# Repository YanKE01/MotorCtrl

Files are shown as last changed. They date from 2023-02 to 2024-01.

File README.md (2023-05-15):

# 光伏水泵评估套件

  

## 开发环境

HardWare：STMicroelectronics Series MCU

SoftWare：KEIL V5/4, CUBEMX , VsCode

## 支持电机

- [x] BLDC+HALL Sensor. Ref: MotorCtrl\SoftWare\BLDC\F407IGT6_HALL
- [x] BLDC SensorLess. Ref: MotorCtrl\SoftWare\BLDC\F407IGT6_NOHALL
- [x] 48V PMSM. Ref: MotorCtrl\SoftWare\PMSM\MCSDK\F401RET6_Pump

## 目录说明

Doc：存放文档

HardWare：存放硬件图纸

Record：存放项目记录

SoftWare：存放软件控制方案

## 开源项目支持

SimpleFoc: [SimpleFoc官网](https://simplefoc.com/)

Ctrl-Foc-Lite: [Ctrl-Foc-Lite项目](https://github.com/peng-zhihui/Ctrl-FOC-Lite)

STM32 MCSDK: [STM32电机库官网](https://www.st.com/content/st_com/en/products/embedded-software/mcu-mpu-embedded-software/stm32-embedded-software/stm32cube-expansion-packages/x-cube-mcsdk.html)

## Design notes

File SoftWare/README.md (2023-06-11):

# SoftWare文件夹说明

* BLDC：存放BLDC电机Hall, SensorLess相关代码
* PMSM：存放PMSM电机无感控制相关代码
* Matlab：存放Matlab仿真实验代码
* Fortior: 存放基于FU6861Q的无感FOC相关代码
* LCM_FOC:存放领芯控制方案
* test:临时测试代码，误动

## Record

母线电压在52V左右时，电机带负载转数拉到3700RPM，电流16A左右，难道电机已经跑到了800W????

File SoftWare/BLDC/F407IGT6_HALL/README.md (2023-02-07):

# 基于正点原子开发版的HALL BLDC驱动

## 开发环境

* CUBEMX: 6.7.0
* KEIL: 5.28.0

## 测试硬件



## 实验效果

* 按下KEY0实现增速
* 按下KEY1实现减速
* 按下KEY2停止电机

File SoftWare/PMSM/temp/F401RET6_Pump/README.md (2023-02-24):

# MCSDK

### 功能指标



### 电机参数修改

* 电机参数：Inc\pmsm_motor_parameters.h
* 电源参数：Inc\power_stage_parameters.h

### 工程问题记录

* TM1650上电不显示：TM1650芯片内部初始化并未完成，所以Delay一段时间，等TM1650内部启动完成。

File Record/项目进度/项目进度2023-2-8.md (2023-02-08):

# BLDC/PMSM开发事项确认

### 人员

人员安排？

### PMSM

* 光伏水泵是否合板？
* 是否按原定的数码管+按键组合?
* 项目时间点确认？
* 优先基于24VPMSM电机进行原理性测试？

### BLDC

以基于正点PCB确认可行性。

* 后续原理图与PCB安排？

### 材料

* 线电感：数字电桥测量，需要购买？

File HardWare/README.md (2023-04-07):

# 硬件问题汇总

- [ ] TM1650面板PCB，以飞线，未修复。
- [ ] 驱动板5V供电部分错误，以割线，未修复。
- [ ] 驱动板三相电流未开窗。
- [ ] 3倍耐压MOS未更换。

### 修改后及时同步仓库

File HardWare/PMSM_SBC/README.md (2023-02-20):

# PMSM_SBC

### 版本迭代

当前版本：PMSM_Driver_V0.16



### 绘制人员

* 设计：严柯
* 绘制：王建
* 审核：傅雷

### 日志

* LMV358以替换TP2412，原LMV358启动失败次数过多，引脚兼容，无需修改PCB

### 其他

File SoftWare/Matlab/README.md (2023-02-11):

# FOC MATLAB仿真

## 1.初期ANTI PARK仿真实验的相关设置

* 模拟电角度增加可以使用Repeating Sequence模块搭建



* 仿真时间与离散化设置







## 2.电流环





电流闭环系统如下：



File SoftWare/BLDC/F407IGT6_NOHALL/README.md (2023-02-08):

# 基于正点原子开发版的BLDC 无感驱动

## 开发环境

* CUBEMX: 6.7.0
* KEIL: 5.28.0

## 测试硬件

* 务必将驱动板板载跳线由HALL<->H&Z 切换至 ==H&Z <-> ZERO==

## 开发记录



顺时针：HallLess的状态为 5 4 6 2 3 1



逆时针：HallLess的状态为 5 1 3 2 6 4



## 实验效果

* 按下KEY0实现逆时针旋转
* 按下KEY1实现顺时针旋转
* 按下KEY2停止电机

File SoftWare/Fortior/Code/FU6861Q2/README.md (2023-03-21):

# Standard Software for Vacuum Cleaners

> 这是基于FU6861Q2的单电阻无感FOC标准吸尘器程序  
> 如有BUG或者优化建议，可提交到标准程序对应的议题

## 适用编译器

- [支持] KeilC51
- [不支持] FTCC

## 适用芯片
- FU6861Q2

## 发布记录

V1.0.0(2022-11-29)
- 初始版本
- 基于FU6861Q2的单电阻无感FOC标准吸尘器程序
---

## 版权说明
> 版权所有©峰岹科技（深圳）股份有限公司（以下简称：峰岹科技）。<br>

> 为改进设计和/或性能，峰岹科技保留对本文档所描述或包含的产品（包括电路、标准元件和/><br>或软件）进行更改的权利。本文档中包含的信息供峰岹科技的客户进行一般性使用。峰岹科技的客户应确保采取适当行动，以使其对峰岹科技产品的使用不侵犯任何专利。峰岹科技尊重第三方的有效专利权，不侵犯或协助他人侵犯该等权利。<br>
> 本文档版权归峰岹科技所有，未经峰岹科技明确书面许可，任何单位及个人不得以任何形式或方式（如电子、机械、磁性、光学、化学、手工操作或其他任何方式），对本文档任何内容进行复制、传播、抄录、存储于检索系统或翻译为任何语种，亦不得更改或删除> 本内容副本中的任何版权或其他声明信息。<br>

> 峰岹科技（深圳）股份有限公司<br>
> 深圳市南山区科技中二路深圳软件园二期11栋2楼203<br>
> 邮编：518057<br>
> 电话：0755-26867710<br>
> 传真：0755-26867715<br>
> 网址：[www.fortiortech.com](https://www.fortiortech.com)

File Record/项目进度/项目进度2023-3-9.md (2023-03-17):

* MOS选型：耐压选择超过三倍。参考样品的选择。

* 时间计划表。
* 散热问题。
* 外观：
  * 铝壳公模，可购买
  * 按照样品来
* 功能测试：按照实物来、实机测试。
* 转速问题：4200RPM为额定点。
* 处理：观测器调整。
  * 电流上去后，观测器没处理好。
  * 库方案没有处理。
* 电机制作粗糙，只能调试。

# 后期进度安排：

1. 外壳设计

2. 走线设计 有参考设计。参照设计

3. MOS管选型

4. 给出电机需要参数

5. 电机加负载 (放在水里) 

6. 电源：兆信。电源串

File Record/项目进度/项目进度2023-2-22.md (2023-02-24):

# 2023-2-22项目进度记录

### 现有问题：

* 转速无法上升到2300以上，疑似11V稳压输出不行。
* 显示面板需要上电复位后，才显示。(以修复PCB错误)

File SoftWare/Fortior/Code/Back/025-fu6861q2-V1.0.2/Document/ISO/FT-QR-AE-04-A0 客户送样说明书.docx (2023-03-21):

客户送样说明书

送样日期：2020年5月2日

1、 基本情况

供 应 方： | 峰岹科技（深圳）股份有限公司 | 工 程 师： | 汤工：13856094270
接 收 方： | 新科空调有限公司 | 工 程 师： | 刘工
项目名称： | 压缩机 | 产品型号： | FU6812L
配件清单： | FU6812L控制板（1pcs）、电机接头线(1条)

二、测试板基本功能描述

序号 | 项目 | 参数 | 序号 | 项目 | 参数
1 | 电机规格型号 | 极对数为3、电阻0.35欧姆，电感为0.00005H | 2 | 负载
3 | 工作电压（V） | 220V交流电 | 4 | 工作电流（A） | 最大10A
其他

三、连线说明

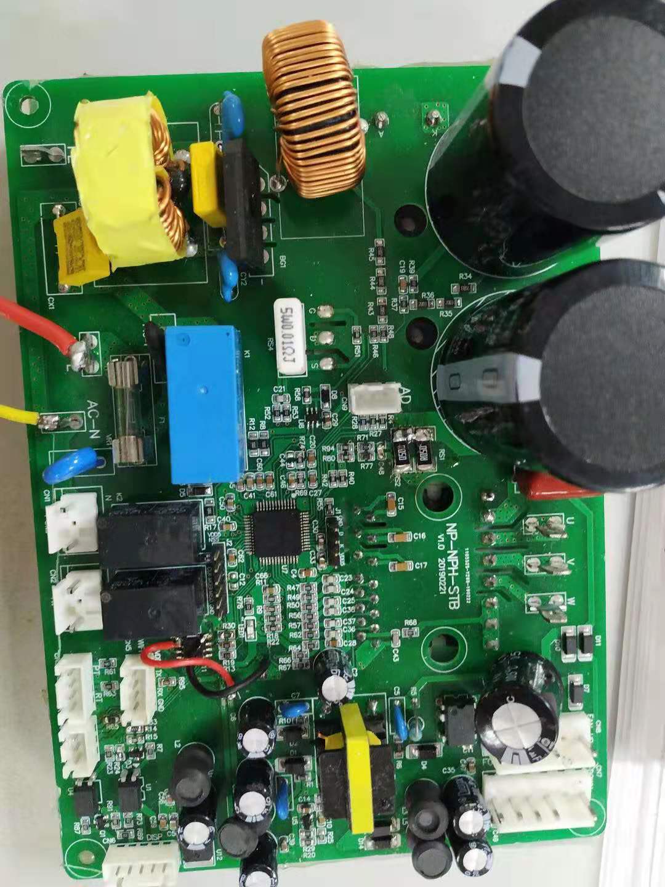
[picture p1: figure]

电机U,V,W相线

220VAC接线端

峰岹科技（深圳）股份有限公司

表单编号：FT-QR-AE-04-A0 流水号：

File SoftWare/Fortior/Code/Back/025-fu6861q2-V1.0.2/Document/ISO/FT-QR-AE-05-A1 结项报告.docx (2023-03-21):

# 项目结项报告

结项日期：2020年12月05日

一、项目结项信息

应用方案描述：新科空调 | 项目当前阶段: 结项
结项原因：客户持续2个月以上无反馈 | 申请人：汤伟
销售审核人： | 应用审核人：

备注：应用方案结项原因有以下几种情况：

（1）符合要求，已经量产；

（2）在方案设计及产品板内部测试阶段遇到无法解决的技术问题；

（3）在客户端测试验证阶段出现无法解决的异常情况；

（4）因性能、价格、交期达不到客户要求；

（5）客户持续2个月以上无反馈；

（6）客户已确认性能符合要求，但未有订单；

（7）其他__________________________。

二、结项清单

客户方案性能设计需求表 | √
应用方案计划表 | √
客户产品板测试报告 | √
客户送样说明书 | √
成功案例介绍PPT（必要时） | ×
烧录文件归档 | ×
原理图&PCB归档 | √

峰岹科技（深圳）股份有限公司

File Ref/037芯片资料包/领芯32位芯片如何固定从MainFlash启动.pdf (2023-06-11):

## 领芯 32 位芯片如何固定从 MainFlash 启动

## 1，确认芯片 BOOT 模式

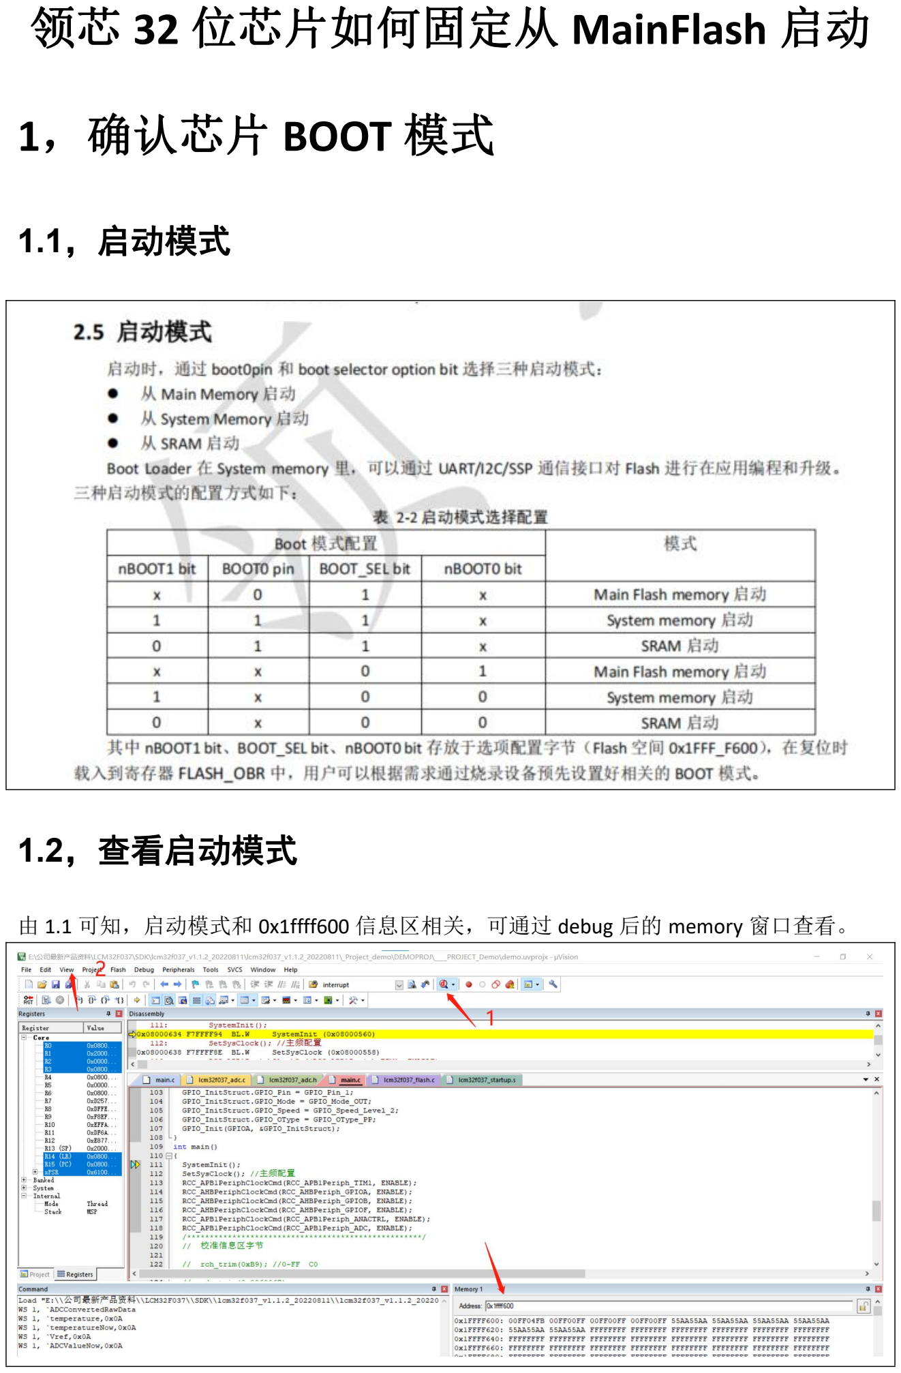
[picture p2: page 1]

1.1，启动模式

1.2，查看启动模式

由 1.1 可知，启动模式和 0x1ffff600 信息区相关，可通过 debug 后的 memory 窗口查看。

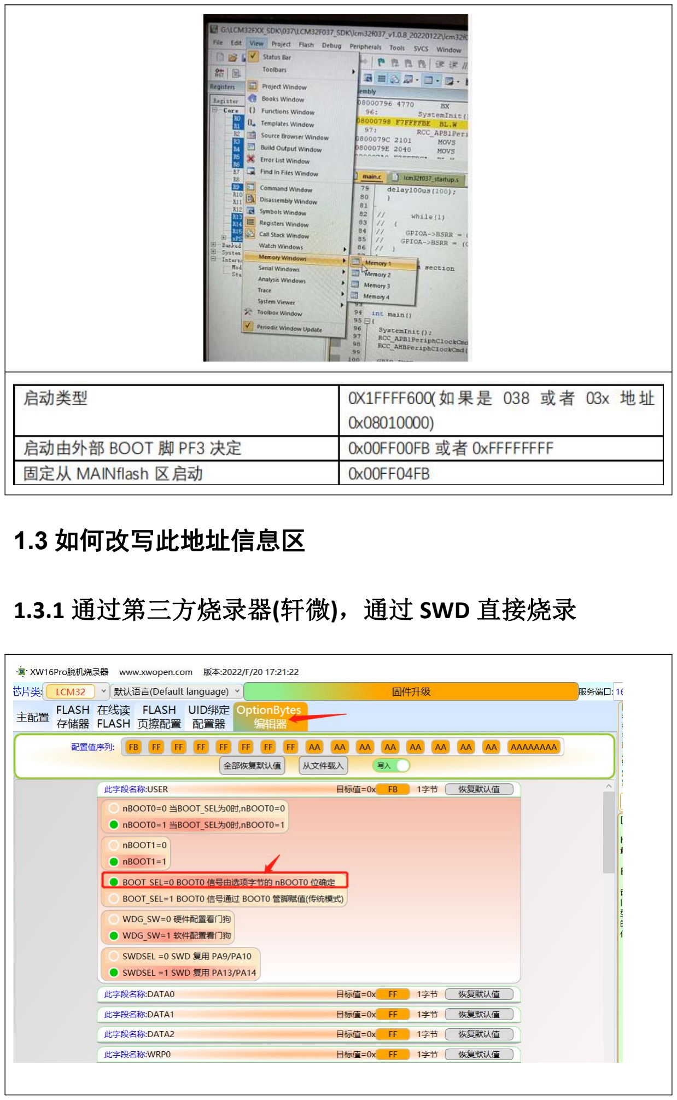
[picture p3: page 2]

### 1.3 如何改写此地址信息区

### 1.3.1 通过第三方烧录器(轩微)，通过 SWD 直接烧录

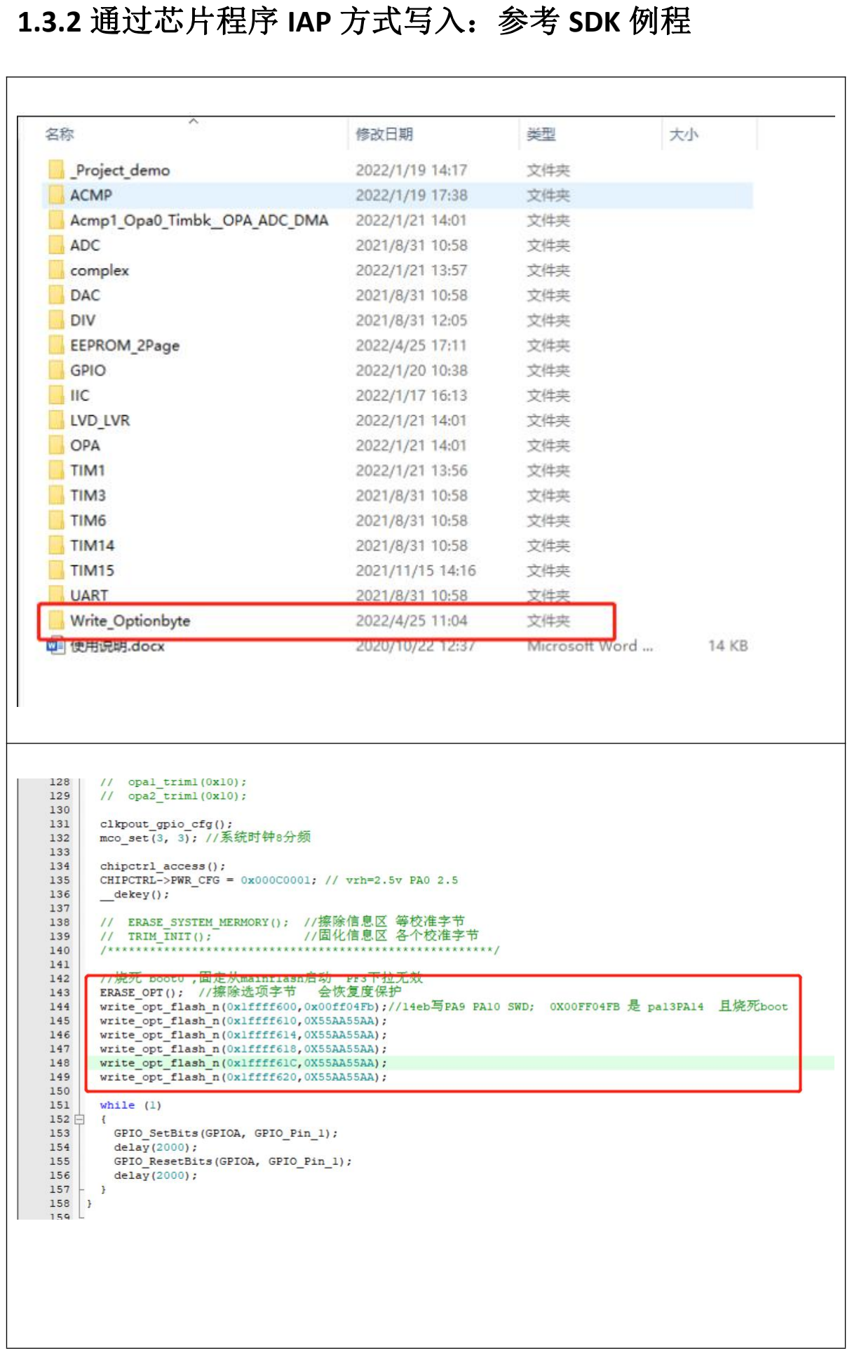
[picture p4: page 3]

### 1.3.2 通过芯片程序 IAP 方式写入：参考 SDK 例程

此方式是程序自写，下载此程序，PF3 拉低，确保此程序正

常运行。运行结束后使用 DEBUG 确认数据。

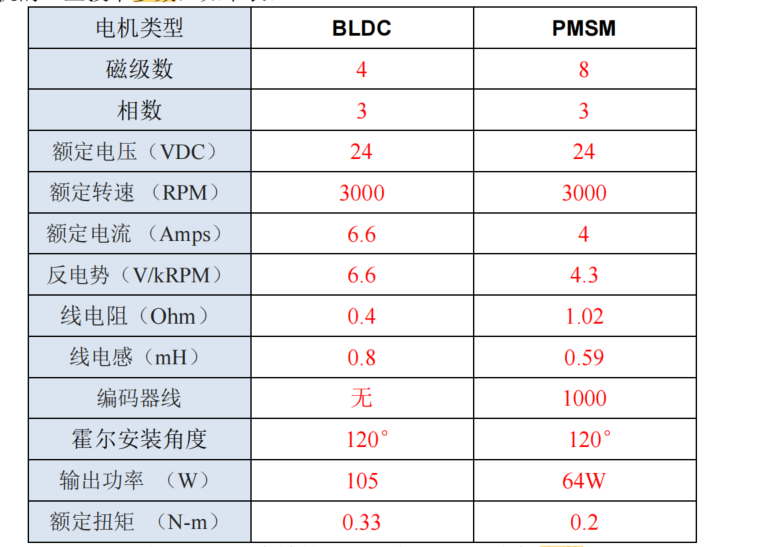
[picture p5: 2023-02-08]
Doc/电机参数/正点原子系列电机.png

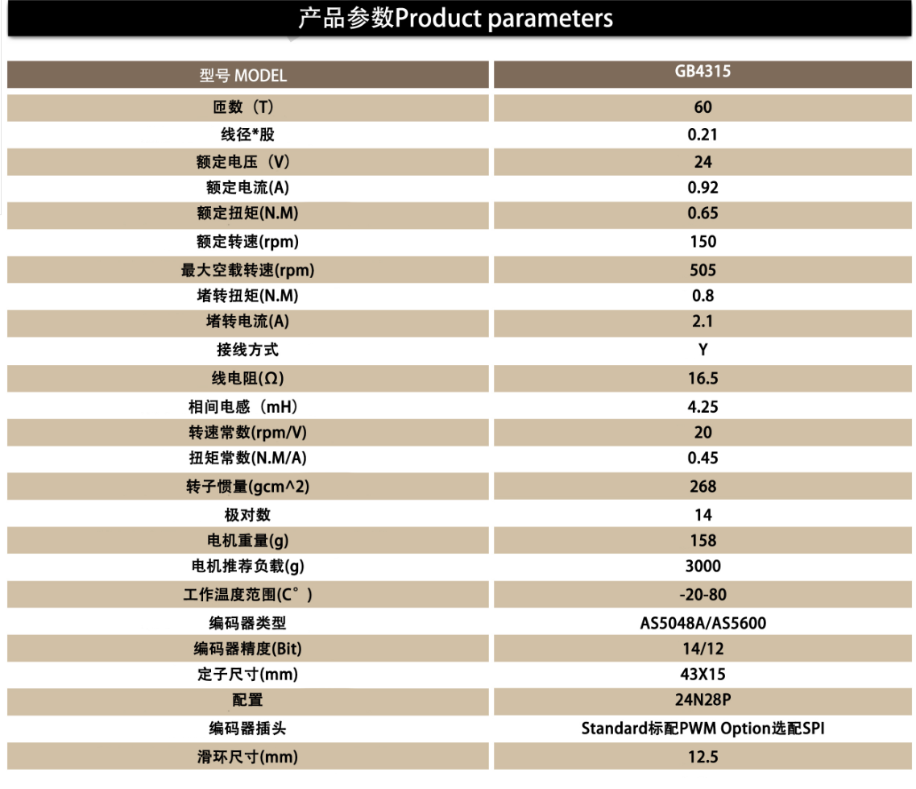
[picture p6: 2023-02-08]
Doc/电机参数/GB4315.png

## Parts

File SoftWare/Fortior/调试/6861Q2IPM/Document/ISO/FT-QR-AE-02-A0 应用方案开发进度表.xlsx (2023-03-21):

 |  | 表单编号： | FT-QR-AE-02-A0
 |  | 流水号：
新科空调项目预期开发进度
一、项目基本情况
项目名称 | 新科空调 | 项目编号 | R10003451
项目经理 | JOHN | 审核人
制作人 | Jack | 制作日期 | 2019-06-10
二、项目进度表
计划进度 | 进度 | 计划完成时间 | 责任人 | 关键里程碑
 | 需求确认 | 2019-06-12 | Jack | 确认客户需求
 | 原理图设计 | 2019-06-15 | Frank | 出原理图
 | PCB Layout | 2019-06-23 | Gavin | 出PCB
 | 物料采购 | 2019-06-25 | Jack | 常规物料采购
 | PCB 投板 | 2019-06-28 | Jack | PCB
 | PCB焊接 | 2019-07-02 | David | 2块焊接板
 | 调试及送样 | 2020-06-01 | Jack | 1块产品板
计划变更说明

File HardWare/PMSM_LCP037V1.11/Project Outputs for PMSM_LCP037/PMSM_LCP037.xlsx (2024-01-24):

Comment | Description | Designator | Footprint | LibRef | Quantity
470uF/25V |  | C100 | 47UF/100V | CapSMT220u_16V | 1
22uF (226) 20% 25V | 贴片电容 | C101 | 0805_C | 0805 22uF (226) 20% 25V | 1
100nF(104) 10% 50V | 贴片电容 | C102, C108, C109 | 0805_C | 0805 100nF(104) 10% 50V | 3
47pF (470) 5% 50V | 贴片电容 | C103 | 0805_C | 0805 47pF (470) 5% 50V | 1
100nF (104) 10% 50V | 贴片电容 | C104, C106, C116, C118, C202, C203, C208 | 0603_C | 0603 100nF (104) 10% 50V | 7
10uF (106) 10% 10V | 贴片电容 | C105, C107, C117, C119 | 0603_C | 0603 10uF (106) 10% 10V | 4
47uF/100V |  | C110 | 47UF/100V | CapSMT220u_16V | 1
2.2uF (225) 10% 50V | 贴片电容 | C111 | 1206_C | 1206 2.2uF (225) 10% 50V | 1
100nF (104) 10% 50V | 贴片电容 | C112 | 1206_C | 1206 100nF (104) 10% 50V | 1
2.2nF (222) 10% 50V | 贴片电容 | C115 | X1/Y1 500V | 0603 2.2nF (222) 10% 50V | 1
10uF (106) 10% 25V | 贴片电容 | C201, C204, C205, C206, C207 | 0805_C | 0805 10uF (106) 10% 25V | 5
100nF (104) 10% 100V | 贴片电容 | C300, C301, C302 | 1206_C | 1206 100nF (104) 10% 50V | 3
100pF (101) 5% 50V | 贴片电容 | C303, C304, C305 | 0805_C | 0805 100pF (101) 5% 50V | 3
1000uF/250V | 电解电容 | C310, C311 | 1000uf/250V | CAP2 | 2
SS310 |  | D100 | SS310 | SS310 | 1
绿灯 0603 | 发光二极管 | D101 | 0603_LED_S1 | 0603 绿灯 | 1
SMF12A |  | D102 | SMF12A - duplicate | SMF12A | 1
SMBJ18A |  | D103 | SMBJ18A | 1N4746A | 1
1N4148WS T4 | 二极管 | D200, D201, D202, D300, D301, D302, D303, D304, D307 | SOD-323 | SOD-323 1N4148WS T4 | 9
CON9 |  | J101 | CON9 9.5mm | CON9 | 1
SWD-KF2510-5P |  | J200 | 2.54_5P_PHI | ST-LINK-SWD | 1
47uH/0650 |  | L100, L101 | 0650_47uH | Inductor | 2
Header 5 | Header, 5-Pin | P201 | XH2.54-5P | Header 5 | 1
NCEP1570 |  | Q100, Q300, Q301, Q302, Q303, Q304, Q305 | IRFB4127 | IRFB4127PBF | 7
330KΩ (3303) ±1% | 贴片电阻 | R100 | 0805_R | 0805 330KΩ (3303) 1% | 1
10KΩ (1002) ±1% | 贴片电阻 | R101, R205 | 0603_R | 0603 10KΩ (1002) 1% | 2
22Ω (22R0) ±1% | 贴片电阻 | R102 | 0805_R | 0805 22Ω (22R0) 1% | 1
23.7KΩ | 贴片电阻 | R103 | 0805_R | 0805 22Ω (22R0) 1% | 1
30mΩ ±1% | 贴片电阻 | R104 | 0603_R | 0603 100KΩ (1003) 1% | 1
200Ω (2000) ±1% | 贴片电阻 | R105, R109 | 1206_R | 1206 300Ω (3000) 1% | 2
20KΩ (2002) ±1% | 贴片电阻 | R106 | 0805_R | 0805 20KΩ (2002) 1% | 1
24KΩ (2402) ±1% | 贴片电阻 | R107 | 1206_R | 1206 0Ω (0R0) 1% | 1
1KΩ (1001) ±1% | 贴片电阻 | R108, R203 | 0805_R | 0805 1KΩ (1001) 1% | 2
10KΩ (1002) ±1% | 贴片电阻 | R112 | 0805_R | 0805 10KΩ (1002) 1% | 1
1KΩ (1001) ±1% | 贴片电阻 | R200, R201 | 0603_R | 0603 1KΩ (1001) 1% | 2
51Ω (51R0) ±1% | 贴片电阻 | R300, R301, R302, R306, R307, R308 | 0805_R | 0805 51Ω (51R0) 1% | 6
100KΩ (1003) ±1% | 贴片电阻 | R303, R304, R305, R309, R310, R311 | 0805_R | 0805 100KΩ (1003) 1% | 6
10mR 2512 |  | R312, R316, R317 | R2512 | Res10K | 3
68Ω (68R0) ±1% | 贴片电阻 | R313, R314, R315, R318, R319, R320 | 0805_R | 0805 68Ω (68R0) 1% | 6
KEY |  | S200 | 按键3*4 | KEY | 1
Test |  | T100, T200 | Testpoint | TestPad | 2
Test |  | T101 | 接地螺丝孔 | TestPad | 1
TX4139 |  | U100 | ESOP8 | TX4139 | 1
LCP037BK32ET8 |  | U200 | LQFP32 | LCP037BT32EU8 | 1
AMS1117-5.0 | 低压差线性稳压(LDO) | VR100, VR101 | SOT-223 | SOT-223 AMS1117-5.0 | 2

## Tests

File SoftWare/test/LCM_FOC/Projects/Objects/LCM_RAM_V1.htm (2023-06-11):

# Static Call Graph for image .\Objects\LCM_RAM_V1.axf

#<CALLGRAPH># ARM Linker, 5060750: Last Updated: Sun Jun 11 15:01:52 2023

### Maximum Stack Usage = 324 bytes + Unknown(Cycles, Untraceable Function Pointers)

### Call chain for Maximum Stack Depth:

SysTick_Handler ⇒ HY_TaskLoop ⇒ HY_Task_50MS_Entry ⇒ ModeUi ⇒ HY_TM1650_ShowFault ⇒ HY_TM1650_SetNumber ⇒ HY_TM1650_SetIndexNumber ⇒ HY_TM1650_Write ⇒ iic_sendByte ⇒ sda_ouput ⇒ GPIO_Init

### Mutually Recursive functions

- NMI_Handler ⇒ NMI_Handler
- SVC_Handler ⇒ SVC_Handler
- PendSV_Handler ⇒ PendSV_Handler
- ADC_Handler ⇒ ADC_Handler

### Function Pointers

- ADC_Handler from lcm32f037_startup.o(.text) referenced from lcm32f037_startup.o(RESET)
- CAN_Handler from lcm32f037_startup.o(.text) referenced from lcm32f037_startup.o(RESET)
- CHIPCTRL_Handler from lcm32f037_startup.o(.text) referenced from lcm32f037_startup.o(RESET)
- COPROC_Handler from lcm32f037_startup.o(.text) referenced from lcm32f037_startup.o(RESET)
- DMAC_CH0_Handler from lcm32f037_startup.o(.text) referenced from lcm32f037_startup.o(RESET)
- DMAC_CH1_2_Handler from user_interrupt.o(i.DMAC_CH1_2_Handler) referenced from lcm32f037_startup.o(RESET)
- DMAC_CH3_5_Handler from lcm32f037_startup.o(.text) referenced from lcm32f037_startup.o(RESET)
- EFLS_Handler from lcm32f037_startup.o(.text) referenced from lcm32f037_startup.o(RESET)
- EXTI0_1_Handler from lcm32f037_startup.o(.text) referenced from lcm32f037_startup.o(RESET)
- EXTI2_3_Handler from lcm32f037_startup.o(.text) referenced from lcm32f037_startup.o(RESET)
- EXTI4_15_Handler from lcm32f037_startup.o(.text) referenced from lcm32f037_startup.o(RESET)
- HardFault_Handler from lcm32f037_startup.o(.text) referenced from lcm32f037_startup.o(RESET)
- I2C0_Handler from lcm32f037_startup.o(.text) referenced from lcm32f037_startup.o(RESET)
- I2C1RVE_Handler from lcm32f037_startup.o(.text) referenced from lcm32f037_startup.o(RESET)
- LCD_ACMP0_2_Handler from lcm32f037_startup.o(.text) referenced from lcm32f037_startup.o(RESET)
- LVD_Handler from lcm32f037_startup.o(.text) referenced from lcm32f037_startup.o(RESET)
- NMI_Handler from lcm32f037_startup.o(.text) referenced from lcm32f037_startup.o(RESET)
- PendSV_Handler from lcm32f037_startup.o(.text) referenced from lcm32f037_startup.o(RESET)
- Reset_Handler from lcm32f037_startup.o(.text) referenced from lcm32f037_startup.o(RESET)
- SSP0_Handler from lcm32f037_startup.o(.text) referenced from lcm32f037_startup.o(RESET)
- SSP1_3RVE_Handler from lcm32f037_startup.o(.text) referenced from lcm32f037_startup.o(RESET)
- SVC_Handler from lcm32f037_startup.o(.text) referenced from lcm32f037_startup.o(RESET)
- SysTick_Handler from user_interrupt.o(i.SysTick_Handler) referenced from lcm32f037_startup.o(RESET)
- SystemInit from lcm32f037_rcc.o(i.SystemInit) referenced from lcm32f037_startup.o(.text)
- TIM14_Handler from lcm32f037_startup.o(.text) referenced from lcm32f037_startup.o(RESET)
- TIM15_Handler from lcm32f037_startup.o(.text) referenced from lcm32f037_startup.o(RESET)
- TIM16_Handler from lcm32f037_startup.o(.text) referenced from lcm32f037_startup.o(RESET)
- TIM17_Handler from lcm32f037_startup.o(.text) referenced from lcm32f037_startup.o(RESET)
- TIM1_CC_Handler from lcm32f037_startup.o(.text) referenced from lcm32f037_startup.o(RESET)
- TIM1_NON_CC_Handler from user_interrupt.o(i.TIM1_NON_CC_Handler) referenced from lcm32f037_startup.o(RESET)
- TIM2_ACMP3_5_PLC_ZC_Handler from lcm32f037_startup.o(.text) referenced from lcm32f037_startup.o(RESET)
- TIM3_Handler from lcm32f037_startup.o(.text) referenced from lcm32f037_startup.o(RESET)
- TIM6_DAC0_2_Handler from lcm32f037_startup.o(.text) referenced from lcm32f037_startup.o(RESET)
- TIM7_DAC3_5_PLC_Handler from lcm32f037_startup.o(.text) referenced from lcm32f037_startup.o(RESET)
- UART0_Handler from user_interrupt.o(i.UART0_Handler) referenced from lcm32f037_startup.o(RESET)
- UART1_Handler from lcm32f037_startup.o(.text) referenced from lcm32f037_startup.o(RESET)
- UART2_5_Handler from lcm32f037_startup.o(.text) referenced from lcm32f037_startup.o(RESET)
- WT_Handler from lcm32f037_startup.o(.text) referenced from lcm32f037_startup.o(RESET)
- WWDG_Handler from lcm32f037_startup.o(.text) referenced from lcm32f037_startup.o(RESET)
- __main from __main.o(!!!main) referenced from lcm32f037_startup.o(.text)

### Global Symbols

__main (Thumb, 8 bytes, Stack size 0 bytes, __main.o(!!!main))

[Calls]

- >> __rt_entry
- >> __scatterload

__scatterload (Thumb, 0 bytes, Stack size unknown bytes, __scatter.o(!!!scatter))

[Called By]

- >> __main

__scatterload_rt2 (Thumb, 52 bytes, Stack size unknown bytes, __scatter.o(!!!scatter), UNUSED)

[Calls]

- >> __rt_entry

__scatterload_rt2_thumb_only (Thumb, 0 bytes, Stack size unknown bytes, __scatter.o(!!!scatter), UNUSED)

__scatterload_null (Thumb, 0 bytes, Stack size unknown bytes, __scatter.o(!!!scatter), UNUSED)

__scatterload_copy (Thumb, 26 bytes, Stack size unknown bytes, __scatter_copy.o(!!handler_copy), UNUSED)

[Calls]

- >> __scatterload_copy

[Called By]

- >> __scatterload_copy

__scatterload_zeroinit (Thumb, 28 bytes, Stack size unknown bytes, __scatter_zi.o(!!handler_zi), UNUSED)

__rt_lib_init (Thumb, 0 bytes, Stack size unknown bytes, libinit.o(.ARM.Collect$$libinit$$00000000))

[Called By]

- >> __rt_entry_li

__rt_lib_init_alloca_1 (Thumb, 0 bytes, Stack size unknown bytes, libinit2.o(.ARM.Collect$$libinit$$0000002E))

__rt_lib_init_argv_1 (Thumb, 0 bytes, Stack size unknown bytes, libinit2.o(.ARM.Collect$$libinit$$0000002C))

__rt_lib_init_atexit_1 (Thumb, 0 bytes, Stack size unknown bytes, libinit2.o(.ARM.Collect$$libinit$$0000001B))

__rt_lib_init_clock_1 (Thumb, 0 bytes, Stack size unknown bytes, libinit2.o(.ARM.Collect$$libinit$$00000021))

__rt_lib_init_cpp_1 (Thumb, 0 bytes, Stack size unknown bytes, libinit2.o(.ARM.Collect$$libinit$$00000032))

__rt_lib_init_exceptions_1 (Thumb, 0 bytes, Stack size unknown bytes, libinit2.o(.ARM.Collect$$libinit$$00000030))

__rt_lib_init_fp_1 (Thumb, 0 bytes, Stack size unknown bytes, libinit2.o(.ARM.Collect$$libinit$$00000002))

__rt_lib_init_fp_trap_1 (Thumb, 0 bytes, Stack size unknown bytes, libinit2.o(.ARM.Collect$$libinit$$0000001F))

__rt_lib_init_getenv_1 (Thumb, 0 bytes, Stack size unknown bytes, libinit2.o(.ARM.Collect$$libinit$$00000023))

__rt_lib_init_heap_1 (Thumb, 0 bytes, Stack size unknown bytes, libinit2.o(.ARM.Collect$$libinit$$0000000A))

__rt_lib_init_lc_collate_1 (Thumb, 0 bytes, Stack size unknown bytes, libinit2.o(.ARM.Collect$$libinit$$00000011))

__rt_lib_init_lc_ctype_1 (Thumb, 0 bytes, Stack size unknown bytes, libinit2.o(.ARM.Collect$$libinit$$00000013))

__rt_lib_init_lc_monetary_1 (Thumb, 0 bytes, Stack size unknown bytes, libinit2.o(.ARM.Collect$$libinit$$00000015))

__rt_lib_init_lc_numeric_1 (Thumb, 0 bytes, Stack size unknown bytes, libinit2.o(.ARM.Collect$$libinit$$00000017))

__rt_lib_init_lc_time_1 (Thumb, 0 bytes, Stack size unknown bytes, libinit2.o(.ARM.Collect$$libinit$$00000019))

__rt_lib_init_preinit_1 (Thumb, 0 bytes, Stack size unknown bytes, libinit2.o(.ARM.Collect$$libinit$$00000004))

__rt_lib_init_rand_1 (Thumb, 0 bytes, Stack size unknown bytes, libinit2.o(.ARM.Collect$$libinit$$0000000E))

__rt_lib_init_return (Thumb, 0 bytes, Stack size unknown bytes, libinit2.o(.ARM.Collect$$libinit$$00000033))

__rt_lib_init_signal_1 (Thumb, 0 bytes, Stack size unknown bytes, libinit2.o(.ARM.Collect$$libinit$$0000001D))

__rt_lib_init_stdio_1 (Thumb, 0 bytes, Stack size unknown bytes, libinit2.o(.ARM.Collect$$libinit$$00000025))

__rt_lib_init_user_alloc_1 (Thumb, 0 bytes, Stack size unknown bytes, libinit2.o(.ARM.Collect$$libinit$$0000000C))

__rt_lib_shutdown (Thumb, 0 bytes, Stack size unknown bytes, libshutdown.o(.ARM.Collect$$libshutdown$$00000000))

[Called By]

- >> __rt_exit_ls

__rt_lib_shutdown_cpp_1 (Thumb, 0 bytes, Stack size unknown bytes, libshutdown2.o(.ARM.Collect$$libshutdown$$00000002))

__rt_lib_shutdown_fp_trap_1 (Thumb, 0 bytes, Stack size unknown bytes, libshutdown2.o(.ARM.Collect$$libshutdown$$00000007))

__rt_lib_shutdown_heap_1 (Thumb, 0 bytes, Stack size unknown bytes, libshutdown2.o(.ARM.Collect$$libshutdown$$0000000F))

__rt_lib_shutdown_return (Thumb, 0 bytes, Stack size unknown bytes, libshutdown2.o(.ARM.Collect$$libshutdown$$00000010))

__rt_lib_shutdown_signal_1 (Thumb, 0 bytes, Stack size unknown bytes, libshutdown2.o(.ARM.Collect$$libshutdown$$0000000A))

__rt_lib_shutdown_stdio_1 (Thumb, 0 bytes, Stack size unknown bytes, libshutdown2.o(.ARM.Collect$$libshutdown$$00000004))

__rt_lib_shutdown_user_alloc_1 (Thumb, 0 bytes, Stack size unknown bytes, libshutdown2.o(.ARM.Collect$$libshutdown$$0000000C))

__rt_entry (Thumb, 0 bytes, Stack size unknown bytes, __rtentry.o(.ARM.Collect$$rtentry$$00000000))

[Called By]

- >> __main
- >> __scatterload_rt2

__rt_entry_presh_1 (Thumb, 0 bytes, Stack size unknown bytes, __rtentry2.o(.ARM.Collect$$rtentry$$00000002))

__rt_entry_sh (Thumb, 0 bytes, Stack size unknown bytes, __rtentry4.o(.ARM.Collect$$rtentry$$00000004))

[Stack]

- Max Depth = 8 + Unknown Stack Size
- Call Chain = __rt_entry_sh ⇒ __user_setup_stackheap

[Calls]

- >> __user_setup_stackheap

__rt_entry_li (Thumb, 0 bytes, Stack size unknown bytes, __rtentry2.o(.ARM.Collect$$rtentry$$0000000A))

[Calls]

- >> __rt_lib_init

__rt_entry_postsh_1 (Thumb, 0 bytes, Stack size unknown bytes, __rtentry2.o(.ARM.Collect$$rtentry$$00000009))

__rt_entry_main (Thumb, 0 bytes, Stack size unknown bytes, __rtentry2.o(.ARM.Collect$$rtentry$$0000000D))

[Stack]

- Max Depth = 208 + Unknown Stack Size
- Call Chain = __rt_entry_main ⇒ main ⇒ UP_vDeviceInit ⇒ US_vSystParaInitPowerup ⇒ MDS_vMotorParaCalc ⇒ __aeabi_ddiv

[Calls]

- >> main
- >> exit

__rt_entry_postli_1 (Thumb, 0 bytes, Stack size unknown bytes, __rtentry2.o(.ARM.Collect$$rtentry$$0000000C))

__rt_exit (Thumb, 0 bytes, Stack size unknown bytes, rtexit.o(.ARM.Collect$$rtexit$$00000000))

[Called By]

- >> exit

__rt_exit_ls (Thumb, 0 bytes, Stack size unknown bytes, rtexit2.o(.ARM.Collect$$rtexit$$00000003))

[Calls]

- >> __rt_lib_shutdown

__rt_exit_prels_1 (Thumb, 0 bytes, Stack size unknown bytes, rtexit2.o(.ARM.Collect$$rtexit$$00000002))

__rt_exit_exit (Thumb, 0 bytes, Stack size unknown bytes, rtexit2.o(.ARM.Collect$$rtexit$$00000004))

[Calls]

- >> _sys_exit

__aeabi_memcpy4 (Thumb, 56 bytes, Stack size 0 bytes, rt_memcpy.o(.emb_text))

[Called By]

- >> ModeUi

__aeabi_memcpy8 (Thumb, 0 bytes, Stack size 0 bytes, rt_memcpy.o(.emb_text), UNUSED)

Reset_Handler (Thumb, 8 bytes, Stack size 0 bytes, lcm32f037_startup.o(.text))
[Address Reference Count : 1]

- lcm32f037_startup.o(RESET)

NMI_Handler (Thumb, 2 bytes, Stack size 0 bytes, lcm32f037_startup.o(.text))

[Calls]

- >> NMI_Handler

[Called By]

- >> NMI_Handler

[Address Reference Count : 1]

- lcm32f037_startup.o(RESET)

HardFault_Handler (Thumb, 2 bytes, Stack size 0 bytes, lcm32f037_startup.o(.text))
[Address Reference Count : 1]

- lcm32f037_startup.o(RESET)

SVC_Handler (Thumb, 2 bytes, Stack size 0 bytes, lcm32f037_startup.o(.text))

[Calls]

- >> SVC_Handler

[Called By]

- >> SVC_Handler

[Address Reference Count : 1]

- lcm32f037_startup.o(RESET)

PendSV_Handler (Thumb, 2 bytes, Stack size 0 bytes, lcm32f037_startup.o(.text))

[Calls]

- >> PendSV_Handler

[Called By]

- >> PendSV_Handler

[Address Reference Count : 1]

- lcm32f037_startup.o(RESET)

ADC_Handler (Thumb, 0 bytes, Stack size 0 bytes, lcm32f037_startup.o(.text))

[Calls]

- >> ADC_Handler

[Called By]

- >> ADC_Handler

[Address Reference Count : 1]

- lcm32f037_startup.o(RESET)

CAN_Handler (Thumb, 0 bytes, Stack size 0 bytes, lcm32f037_startup.o(.text))
[Address Reference Count : 1]

- lcm32f037_startup.o(RESET)

CHIPCTRL_Handler (Thumb, 0 bytes, Stack size 0 bytes, lcm32f037_startup.o(.text))
[Address Reference Count : 1]

- lcm32f037_startup.o(RESET)

COPROC_Handler (Thumb, 0 bytes, Stack size 0 bytes, lcm32f037_startup.o(.text))
[Address Reference Count : 1]

- lcm32f037_startup.o(RESET)

DMAC_CH0_Handler (Thumb, 0 bytes, Stack size 0 bytes, lcm32f037_startup.o(.text))
[Address Reference Count : 1]

- lcm32f037_startup.o(RESET)

DMAC_CH3_5_Handler (Thumb, 0 bytes, Stack size 0 bytes, lcm32f037_startup.o(.text))
[Address Reference Count : 1]

- lcm32f037_startup.o(RESET)

EFLS_Handler (Thumb, 0 bytes, Stack size 0 bytes, lcm32f037_startup.o(.text))
[Address Reference Count : 1]

- lcm32f037_startup.o(RESET)

EXTI0_1_Handler (Thumb, 0 bytes, Stack size 0 bytes, lcm32f037_startup.o(.text))
[Address Reference Count : 1]

- lcm32f037_startup.o(RESET)

EXTI2_3_Handler (Thumb, 0 bytes, Stack size 0 bytes, lcm32f037_startup.o(.text))
[Address Reference Count : 1]

- lcm32f037_startup.o(RESET)

EXTI4_15_Handler (Thumb, 0 bytes, Stack size 0 bytes, lcm32f037_startup.o(.text))
[Address Reference Count : 1]

- lcm32f037_startup.o(RESET)

I2C0_Handler (Thumb, 0 bytes, Stack size 0 bytes, lcm32f037_startup.o(.text))
[Address Reference Count : 1]

- lcm32f037_startup.o(RESET)

I2C1RVE_Handler (Thumb, 0 bytes, Stack size 0 bytes, lcm32f037_startup.o(.text))
[Address Reference Count : 1]

- lcm32f037_startup.o(RESET)

LCD_ACMP0_2_Handler (Thumb, 0 bytes, Stack size 0 bytes, lcm32f037_startup.o(.text))
[Address Reference Count : 1]

- lcm32f037_startup.o(RESET)

LVD_Handler (Thumb, 0 bytes, Stack size 0 bytes, lcm32f037_startup.o(.text))
[Address Reference Count : 1]

- lcm32f037_startup.o(RESET)

SSP0_Handler (Thumb, 0 bytes, Stack size 0 bytes, lcm32f037_startup.o(.text))
[Address Reference Count : 1]

- lcm32f037_startup.o(RESET)

SSP1_3RVE_Handler (Thumb, 0 bytes, Stack size 0 bytes, lcm32f037_startup.o(.text))
[Address Reference Count : 1]

- lcm32f037_startup.o(RESET)

TIM14_Handler (Thumb, 0 bytes, Stack size 0 bytes, lcm32f037_startup.o(.text))
[Address Reference Count : 1]

- lcm32f037_startup.o(RESET)

TIM15_Handler (Thumb, 0 bytes, Stack size 0 bytes, lcm32f037_startup.o(.text))
[Address Reference Count : 1]

- lcm32f037_startup.o(RESET)

TIM16_Handler (Thumb, 0 bytes, Stack size 0 bytes, lcm32f037_startup.o(.text))
[Address Reference Count : 1]

- lcm32f037_startup.o(RESET)

TIM17_Handler (Thumb, 0 bytes, Stack size 0 bytes, lcm32f037_startup.o(.text))
[Address Reference Count : 1]

- lcm32f037_startup.o(RESET)

TIM1_CC_Handler (Thumb, 0 bytes, Stack size 0 bytes, lcm32f037_startup.o(.text))
[Address Reference Count : 1]

- lcm32f037_startup.o(RESET)

TIM2_ACMP3_5_PLC_ZC_Handler (Thumb, 0 bytes, Stack size 0 bytes, lcm32f037_startup.o(.text))
[Address Reference Count : 1]

- lcm32f037_startup.o(RESET)

TIM3_Handler (Thumb, 0 bytes, Stack size 0 bytes, lcm32f037_startup.o(.text))
[Address Reference Count : 1]

- lcm32f037_startup.o(RESET)

TIM6_DAC0_2_Handler (Thumb, 0 bytes, Stack size 0 bytes, lcm32f037_startup.o(.text))
[Address Reference Count : 1]

- lcm32f037_startup.o(RESET)

TIM7_DAC3_5_PLC_Handler (Thumb, 0 bytes, Stack size 0 bytes, lcm32f037_startup.o(.text))
[Address Reference Count : 1]

- lcm32f037_startup.o(RESET)

UART1_Handler (Thumb, 0 bytes, Stack size 0 bytes, lcm32f037_startup.o(.text))
[Address Reference Count : 1]

- lcm32f037_startup.o(RESET)

UART2_5_Handler (Thumb, 0 bytes, Stack size 0 bytes, lcm32f037_startup.o(.text))
[Address Reference Count : 1]

- lcm32f037_startup.o(RESET)

WT_Handler (Thumb, 0 bytes, Stack size 0 bytes, lcm32f037_startup.o(.text))
[Address Reference Count : 1]

- lcm32f037_startup.o(RESET)

WWDG_Handler (Thumb, 0 bytes, Stack size 0 bytes, lcm32f037_startup.o(.text))
[Address Reference Count : 1]

- lcm32f037_startup.o(RESET)

__user_initial_stackheap (Thumb, 10 bytes, Stack size 0 bytes, lcm32f037_startup.o(.text))

[Called By]

- >> __user_setup_stackheap

__aeabi_lmul (Thumb, 48 bytes, Stack size 12 bytes, llmul.o(.text))

[Stack]

- Max Depth = 12
- Call Chain = __aeabi_lmul

[Called By]

- >> MDS_vOBRestarting
- >> MDS_vOBPosObserver

_ll_mul (Thumb, 0 bytes, Stack size 12 bytes, llmul.o(.text), UNUSED)

__aeabi_uldivmod (Thumb, 258 bytes, Stack size 32 bytes, lludiv.o(.text))

[Stack]

- Max Depth = 32
- Call Chain = __aeabi_uldivmod

[Called By]

- >> MDS_vOtherInitFromUserSetting
- >> MDS_vNoWaterCal

_ll_udiv (Thumb, 0 bytes, Stack size 32 bytes, lludiv.o(.text), UNUSED)

__aeabi_uidiv (Thumb, 0 bytes, Stack size 0 bytes, aeabi_sdiv.o(.text), UNUSED)

__aeabi_uidivmod (Thumb, 20 bytes, Stack size 0 bytes, aeabi_sdiv.o(.text))

[Called By]

- >> MDS_vMotorParaCalc
- >> RCC_GetClockFreq
- >> MDS_vOtherInitFromUserSetting
- >> HY_TM1650_SetNumber
- >> ModeUiPageProcess

__aeabi_idiv (Thumb, 0 bytes, Stack size 8 bytes, aeabi_sdiv.o(.text), UNUSED)

__aeabi_idivmod (Thumb, 326 bytes, Stack size 8 bytes, aeabi_sdiv.o(.text))

[Stack]

- Max Depth = 8
- Call Chain = __aeabi_idivmod

[Called By]

- >> MDS_vMotorParaCalc
- >> MDS_vOtherInitFromUserSetting
- >> HY_TaskLoop
- >> HY_TM1650_SetFloat
- >> ModeUi

__use_two_region_memory (Thumb, 2 bytes, Stack size 0 bytes, heapauxi.o(.text), UNUSED)

__rt_heap_escrow$2region (Thumb, 2 bytes, Stack size 0 bytes, heapauxi.o(.text), UNUSED)

__rt_heap_expand$2region (Thumb, 2 bytes, Stack size 0 bytes, heapauxi.o(.text), UNUSED)

__aeabi_d2f (Thumb, 0 bytes, Stack size 12 bytes, d2f.o(.text))

[Stack]

- Max Depth = 12
- Call Chain = __aeabi_d2f

[Called By]

- >> MDS_vMotorParaCalc

_d2f (Thumb, 120 bytes, Stack size 12 bytes, d2f.o(.text), UNUSED)

__aeabi_dadd (Thumb, 0 bytes, Stack size 8 bytes, daddsub.o(.text))

[Stack]

- Max Depth = 8
- Call Chain = __aeabi_dadd

[Called By]

- >> HY_Task_1S_Entry

_dadd (Thumb, 26 bytes, Stack size 8 bytes, daddsub.o(.text), UNUSED)

[Calls]

- >> _dsub1
- >> _dadd1

__aeabi_dsub (Thumb, 0 bytes, Stack size 8 bytes, daddsub.o(.text), UNUSED)

_dsub (Thumb, 22 bytes, Stack size 8 bytes, daddsub.o(.text), UNUSED)

[Calls]

- >> _dsub1
- >> _dadd1

__aeabi_drsub (Thumb, 0 bytes, Stack size 16 bytes, daddsub.o(.text), UNUSED)

_drsb (Thumb, 28 bytes, Stack size 16 bytes, daddsub.o(.text), UNUSED)

[Calls]

- >> _dsub1
- >> _dadd1

__aeabi_ddiv (Thumb, 0 bytes, Stack size 64 bytes, ddiv.o(.text))

[Stack]

- Max Depth = 64
- Call Chain = __aeabi_ddiv

[Called By]

- >> MDS_vRampInit
- >> MDS_vMotorParaCalc
- >> MDS_vOtherInitFromUserSetting
- >> HY_SetPumpMechanicalSpeed

_ddiv (Thumb, 1072 bytes, Stack size 64 bytes, ddiv.o(.text), UNUSED)

[Called By]

- >> _drdiv

_drdiv (Thumb, 20 bytes, Stack size 16 bytes, ddiv.o(.text), UNUSED)

[Calls]

- >> _ddiv

__aeabi_d2iz (Thumb, 0 bytes, Stack size 12 bytes, dfixi.o(.text))

[Stack]

- Max Depth = 12
- Call Chain = __aeabi_d2iz

[Called By]

- >> MDS_vSpdPIRegulatorIQ24Init
- >> MDS_vRampInit
- >> MDS_vFluxWeakeningInit
- >> MDS_vCurrentControllerCalc
- >> MDS_vConstantPowerInit
- >> MDS_vMotorParaCalc
- >> MDS_vOtherInitFromUserSetting

_dfix (Thumb, 98 bytes, Stack size 12 bytes, dfixi.o(.text), UNUSED)

__aeabi_d2uiz (Thumb, 0 bytes, Stack size 8 bytes, dfixui.o(.text))

[Stack]

- Max Depth = 8
- Call Chain = __aeabi_d2uiz

[Called By]

- >> MDS_vMotorParaCalc
- >> HY_SetPumpMechanicalSpeed
- >> HY_Task_1S_Entry

_dfixu (Thumb, 68 bytes, Stack size 8 bytes, dfixui.o(.text), UNUSED)

__aeabi_i2d_normalise (Thumb, 66 bytes, Stack size 0 bytes, dflti.o(.text))

[Called By]

- >> __aeabi_ui2d
- >> __aeabi_i2d

__aeabi_i2d (Thumb, 16 bytes, Stack size 0 bytes, dflti.o(.text), UNUSED)

[Calls]

- >> __aeabi_i2d_normalise

_dflt (Thumb, 0 bytes, Stack size 0 bytes, dflti.o(.text), UNUSED)

__aeabi_ui2d (Thumb, 6 bytes, Stack size 0 bytes, dflti.o(.text))

[Calls]

- >> __aeabi_i2d_normalise

[Called By]

- >> MDS_vMotorParaCalc
- >> MDS_vOtherInitFromUserSetting
- >> HY_SetPumpMechanicalSpeed
- >> HY_Task_1S_Entry

_dfltu (Thumb, 0 bytes, Stack size 0 bytes, dflti.o(.text), UNUSED)

__aeabi_dmul (Thumb, 0 bytes, Stack size 56 bytes, dmul.o(.text))

[Stack]

- Max Depth = 56
- Call Chain = __aeabi_dmul

[Called By]

- >> MDS_vMotorParaCalc
- >> MDS_vOtherInitFromUserSetting
- >> HY_SetPumpMechanicalSpeed
- >> HY_Task_1S_Entry

_dmul (Thumb, 558 bytes, Stack size 56 bytes, dmul.o(.text), UNUSED)

__ARM_scalbn (Thumb, 84 bytes, Stack size 16 bytes, dscalbn.o(.text))

[Stack]

- Max Depth = 16
- Call Chain = __ARM_scalbn

[Called By]

- >> MDS_vSpdPIRegulatorIQ24Init
- >> MDS_vFluxWeakeningInit
- >> MDS_vCurrentControllerCalc
- >> MDS_vConstantPowerInit
- >> MDS_vMotorParaCalc
- >> MDS_vOtherInitFromUserSetting
- >> HY_Task_1S_Entry

__aeabi_f2d (Thumb, 0 bytes, Stack size 0 bytes, f2d.o(.text))

[Called By]

- >> MDS_vSpdPIRegulatorIQ24Init
- >> MDS_vRampInit
- >> MDS_vFluxWeakeningInit
- >> MDS_vCurrentControllerCalc
- >> MDS_vConstantPowerInit
- >> MDS_vMotorParaCalc
- >> MDS_vOtherInitFromUserSetting

_f2d (Thumb, 80 bytes, Stack size 0 bytes, f2d.o(.text), UNUSED)

__aeabi_fdiv (Thumb, 0 bytes, Stack size 20 bytes, fdiv.o(.text))

[Stack]

- Max Depth = 20
- Call Chain = __aeabi_fdiv

[Called By]

- >> MDS_vSpdPIRegulatorIQ24Init
- >> MDS_vFluxWeakeningInit
- >> MDS_vCurrentControllerCalc
- >> MDS_vConstantPowerInit
- >> US_vGlobalVariablesInit
- >> MDS_vMotorParaCalc
- >> MDS_vOtherInitFromUserSetting
- >> MDS_vUdcSwitchCheck

_fdiv (Thumb, 334 bytes, Stack size 20 bytes, fdiv.o(.text), UNUSED)

[Called By]

- >> _frdiv

_frdiv (Thumb, 8 bytes, Stack size 0 bytes, fdiv.o(.text), UNUSED)

[Calls]

- >> _fdiv

__aeabi_f2iz (Thumb, 0 bytes, Stack size 8 bytes, ffixi.o(.text))

[Stack]

- Max Depth = 8
- Call Chain = __aeabi_f2iz

[Called By]

- >> MDS_vCurrentControllerCalc
- >> US_vGlobalVariablesInit
- >> MDS_vMotorParaCalc
- >> MDS_vUdcSwitchCheck
- >> HY_TM1650_SetFloat

_ffix (Thumb, 76 bytes, Stack size 8 bytes, ffixi.o(.text), UNUSED)

__aeabi_f2uiz (Thumb, 0 bytes, Stack size 0 bytes, ffixui.o(.text))

[Called By]

- >> US_vHardwareOverCurCalcAMP

_ffixu (Thumb, 48 bytes, Stack size 0 bytes, ffixui.o(.text), UNUSED)

__aeabi_i2f_normalise (Thumb, 72 bytes, Stack size 0 bytes, fflti.o(.text))

[Called By]

- >> __aeabi_ui2f
- >> __aeabi_i2f

__aeabi_i2f (Thumb, 16 bytes, Stack size 0 bytes, fflti.o(.text))

[Calls]

- >> __aeabi_i2f_normalise

[Called By]

- >> HY_TM1650_SetFloat

_fflt (Thumb, 0 bytes, Stack size 0 bytes, fflti.o(.text), UNUSED)

__aeabi_ui2f (Thumb, 6 bytes, Stack size 0 bytes, fflti.o(.text))

[Calls]

- >> __aeabi_i2f_normalise

[Called By]

- >> MDS_vMotorParaCalc
- >> MDS_vOtherInitFromUserSetting

_ffltu (Thumb, 0 bytes, Stack size 0 bytes, fflti.o(.text), UNUSED)

__ARM_scalbnf (Thumb, 64 bytes, Stack size 8 bytes, fscalbn.o(.text))

[Stack]

- Max Depth = 8
- Call Chain = __ARM_scalbnf

[Called By]

- >> US_vGlobalVariablesInit
- >> MDS_vMotorParaCalc
- >> MDS_vUdcSwitchCheck

__user_setup_stackheap (Thumb, 62 bytes, Stack size 8 bytes, sys_stackheap_outer.o(.text))

[Stack]

- Max Depth = 8
- Call Chain = __user_setup_stackheap

[Calls]

- >> __user_perproc_libspace
- >> __user_initial_stackheap

[Called By]

- >> __rt_entry_sh

exit (Thumb, 16 bytes, Stack size 8 bytes, exit.o(.text))

[Stack]

- Max Depth = 8 + Unknown Stack Size
- Call Chain = exit

[Calls]

- >> __rt_exit
- >> _call_atexit_fns (Weak Reference)

[Called By]

- >> __rt_entry_main

__user_libspace (Thumb, 8 bytes, Stack size 0 bytes, libspace.o(.text), UNUSED)

__user_perproc_libspace (Thumb, 0 bytes, Stack size 0 bytes, libspace.o(.text))

[Called By]

- >> __user_setup_stackheap

__user_perthread_libspace (Thumb, 0 bytes, Stack size 0 bytes, libspace.o(.text), UNUSED)

_sys_exit (Thumb, 8 bytes, Stack size 0 bytes, sys_exit.o(.text))

[Called By]

- >> __rt_exit_exit

__I$use$semihosting (Thumb, 0 bytes, Stack size 0 bytes, use_no_semi.o(.text), UNUSED)

__use_no_semihosting_swi (Thumb, 2 bytes, Stack size 0 bytes, use_no_semi.o(.text), UNUSED)

__semihosting_library_function (Thumb, 0 bytes, Stack size unknown bytes, indicate_semi.o(.text), UNUSED)

ADC_ChannelConfig (Thumb, 24 bytes, Stack size 12 bytes, lcm32f037_adc.o(i.ADC_ChannelConfig))

[Stack]

- Max Depth = 12
- Call Chain = ADC_ChannelConfig

[Called By]
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

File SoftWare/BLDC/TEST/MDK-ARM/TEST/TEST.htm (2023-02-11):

# Static Call Graph for image TEST\TEST.axf

#<CALLGRAPH># ARM Linker, 5060750: Last Updated: Thu Feb 09 16:10:55 2023

### Maximum Stack Usage = 176 bytes + Unknown(Cycles, Untraceable Function Pointers)

### Call chain for Maximum Stack Depth:

main ⇒ SystemClock_Config ⇒ HAL_RCC_ClockConfig ⇒ HAL_RCC_GetSysClockFreq ⇒ __aeabi_uldivmod

### Mutually Recursive functions

- ADC_IRQHandler ⇒ ADC_IRQHandler
- BusFault_Handler ⇒ BusFault_Handler
- HardFault_Handler ⇒ HardFault_Handler
- MemManage_Handler ⇒ MemManage_Handler
- UsageFault_Handler ⇒ UsageFault_Handler

### Function Pointers

- ADC_IRQHandler from startup_stm32f407xx.o(.text) referenced from startup_stm32f407xx.o(RESET)
- BusFault_Handler from stm32f4xx_it.o(i.BusFault_Handler) referenced from startup_stm32f407xx.o(RESET)
- CAN1_RX0_IRQHandler from startup_stm32f407xx.o(.text) referenced from startup_stm32f407xx.o(RESET)
- CAN1_RX1_IRQHandler from startup_stm32f407xx.o(.text) referenced from startup_stm32f407xx.o(RESET)
- CAN1_SCE_IRQHandler from startup_stm32f407xx.o(.text) referenced from startup_stm32f407xx.o(RESET)
- CAN1_TX_IRQHandler from startup_stm32f407xx.o(.text) referenced from startup_stm32f407xx.o(RESET)
- CAN2_RX0_IRQHandler from startup_stm32f407xx.o(.text) referenced from startup_stm32f407xx.o(RESET)
- CAN2_RX1_IRQHandler from startup_stm32f407xx.o(.text) referenced from startup_stm32f407xx.o(RESET)
- CAN2_SCE_IRQHandler from startup_stm32f407xx.o(.text) referenced from startup_stm32f407xx.o(RESET)
- CAN2_TX_IRQHandler from startup_stm32f407xx.o(.text) referenced from startup_stm32f407xx.o(RESET)
- DCMI_IRQHandler from startup_stm32f407xx.o(.text) referenced from startup_stm32f407xx.o(RESET)
- DMA1_Stream0_IRQHandler from startup_stm32f407xx.o(.text) referenced from startup_stm32f407xx.o(RESET)
- DMA1_Stream1_IRQHandler from startup_stm32f407xx.o(.text) referenced from startup_stm32f407xx.o(RESET)
- DMA1_Stream2_IRQHandler from startup_stm32f407xx.o(.text) referenced from startup_stm32f407xx.o(RESET)
- DMA1_Stream3_IRQHandler from startup_stm32f407xx.o(.text) referenced from startup_stm32f407xx.o(RESET)
- DMA1_Stream4_IRQHandler from startup_stm32f407xx.o(.text) referenced from startup_stm32f407xx.o(RESET)
- DMA1_Stream5_IRQHandler from startup_stm32f407xx.o(.text) referenced from startup_stm32f407xx.o(RESET)
- DMA1_Stream6_IRQHandler from startup_stm32f407xx.o(.text) referenced from startup_stm32f407xx.o(RESET)
- DMA1_Stream7_IRQHandler from startup_stm32f407xx.o(.text) referenced from startup_stm32f407xx.o(RESET)
- DMA2_Stream0_IRQHandler from startup_stm32f407xx.o(.text) referenced from startup_stm32f407xx.o(RESET)
- DMA2_Stream1_IRQHandler from startup_stm32f407xx.o(.text) referenced from startup_stm32f407xx.o(RESET)
- DMA2_Stream2_IRQHandler from startup_stm32f407xx.o(.text) referenced from startup_stm32f407xx.o(RESET)
- DMA2_Stream3_IRQHandler from startup_stm32f407xx.o(.text) referenced from startup_stm32f407xx.o(RESET)
- DMA2_Stream4_IRQHandler from startup_stm32f407xx.o(.text) referenced from startup_stm32f407xx.o(RESET)
- DMA2_Stream5_IRQHandler from startup_stm32f407xx.o(.text) referenced from startup_stm32f407xx.o(RESET)
- DMA2_Stream6_IRQHandler from startup_stm32f407xx.o(.text) referenced from startup_stm32f407xx.o(RESET)
- DMA2_Stream7_IRQHandler from startup_stm32f407xx.o(.text) referenced from startup_stm32f407xx.o(RESET)
- DebugMon_Handler from stm32f4xx_it.o(i.DebugMon_Handler) referenced from startup_stm32f407xx.o(RESET)
- ETH_IRQHandler from startup_stm32f407xx.o(.text) referenced from startup_stm32f407xx.o(RESET)
- ETH_WKUP_IRQHandler from startup_stm32f407xx.o(.text) referenced from startup_stm32f407xx.o(RESET)
- EXTI0_IRQHandler from startup_stm32f407xx.o(.text) referenced from startup_stm32f407xx.o(RESET)
- EXTI15_10_IRQHandler from startup_stm32f407xx.o(.text) referenced from startup_stm32f407xx.o(RESET)
- EXTI1_IRQHandler from startup_stm32f407xx.o(.text) referenced from startup_stm32f407xx.o(RESET)
- EXTI2_IRQHandler from startup_stm32f407xx.o(.text) referenced from startup_stm32f407xx.o(RESET)
- EXTI3_IRQHandler from startup_stm32f407xx.o(.text) referenced from startup_stm32f407xx.o(RESET)
- EXTI4_IRQHandler from startup_stm32f407xx.o(.text) referenced from startup_stm32f407xx.o(RESET)
- EXTI9_5_IRQHandler from startup_stm32f407xx.o(.text) referenced from startup_stm32f407xx.o(RESET)
- FLASH_IRQHandler from startup_stm32f407xx.o(.text) referenced from startup_stm32f407xx.o(RESET)
- FMC_IRQHandler from startup_stm32f407xx.o(.text) referenced from startup_stm32f407xx.o(RESET)
- FPU_IRQHandler from startup_stm32f407xx.o(.text) referenced from startup_stm32f407xx.o(RESET)
- HASH_RNG_IRQHandler from startup_stm32f407xx.o(.text) referenced from startup_stm32f407xx.o(RESET)
- HardFault_Handler from stm32f4xx_it.o(i.HardFault_Handler) referenced from startup_stm32f407xx.o(RESET)
- I2C1_ER_IRQHandler from startup_stm32f407xx.o(.text) referenced from startup_stm32f407xx.o(RESET)
- I2C1_EV_IRQHandler from startup_stm32f407xx.o(.text) referenced from startup_stm32f407xx.o(RESET)
- I2C2_ER_IRQHandler from startup_stm32f407xx.o(.text) referenced from startup_stm32f407xx.o(RESET)
- I2C2_EV_IRQHandler from startup_stm32f407xx.o(.text) referenced from startup_stm32f407xx.o(RESET)
- I2C3_ER_IRQHandler from startup_stm32f407xx.o(.text) referenced from startup_stm32f407xx.o(RESET)
- I2C3_EV_IRQHandler from startup_stm32f407xx.o(.text) referenced from startup_stm32f407xx.o(RESET)
- MemManage_Handler from stm32f4xx_it.o(i.MemManage_Handler) referenced from startup_stm32f407xx.o(RESET)
- NMI_Handler from stm32f4xx_it.o(i.NMI_Handler) referenced from startup_stm32f407xx.o(RESET)
- OTG_FS_IRQHandler from startup_stm32f407xx.o(.text) referenced from startup_stm32f407xx.o(RESET)
- OTG_FS_WKUP_IRQHandler from startup_stm32f407xx.o(.text) referenced from startup_stm32f407xx.o(RESET)
- OTG_HS_EP1_IN_IRQHandler from startup_stm32f407xx.o(.text) referenced from startup_stm32f407xx.o(RESET)
- OTG_HS_EP1_OUT_IRQHandler from startup_stm32f407xx.o(.text) referenced from startup_stm32f407xx.o(RESET)
- OTG_HS_IRQHandler from startup_stm32f407xx.o(.text) referenced from startup_stm32f407xx.o(RESET)
- OTG_HS_WKUP_IRQHandler from startup_stm32f407xx.o(.text) referenced from startup_stm32f407xx.o(RESET)
- PVD_IRQHandler from startup_stm32f407xx.o(.text) referenced from startup_stm32f407xx.o(RESET)
- PendSV_Handler from stm32f4xx_it.o(i.PendSV_Handler) referenced from startup_stm32f407xx.o(RESET)
- RCC_IRQHandler from startup_stm32f407xx.o(.text) referenced from startup_stm32f407xx.o(RESET)
- RTC_Alarm_IRQHandler from startup_stm32f407xx.o(.text) referenced from startup_stm32f407xx.o(RESET)
- RTC_WKUP_IRQHandler from startup_stm32f407xx.o(.text) referenced from startup_stm32f407xx.o(RESET)
- Reset_Handler from startup_stm32f407xx.o(.text) referenced from startup_stm32f407xx.o(RESET)
- SDIO_IRQHandler from startup_stm32f407xx.o(.text) referenced from startup_stm32f407xx.o(RESET)
- SPI1_IRQHandler from startup_stm32f407xx.o(.text) referenced from startup_stm32f407xx.o(RESET)
- SPI2_IRQHandler from startup_stm32f407xx.o(.text) referenced from startup_stm32f407xx.o(RESET)
- SPI3_IRQHandler from startup_stm32f407xx.o(.text) referenced from startup_stm32f407xx.o(RESET)
- SVC_Handler from stm32f4xx_it.o(i.SVC_Handler) referenced from startup_stm32f407xx.o(RESET)
- SysTick_Handler from stm32f4xx_it.o(i.SysTick_Handler) referenced from startup_stm32f407xx.o(RESET)
- SystemInit from system_stm32f4xx.o(i.SystemInit) referenced from startup_stm32f407xx.o(.text)
- TAMP_STAMP_IRQHandler from startup_stm32f407xx.o(.text) referenced from startup_stm32f407xx.o(RESET)
- TIM1_BRK_TIM9_IRQHandler from startup_stm32f407xx.o(.text) referenced from startup_stm32f407xx.o(RESET)
- TIM1_CC_IRQHandler from startup_stm32f407xx.o(.text) referenced from startup_stm32f407xx.o(RESET)
- TIM1_TRG_COM_TIM11_IRQHandler from startup_stm32f407xx.o(.text) referenced from startup_stm32f407xx.o(RESET)
- TIM1_UP_TIM10_IRQHandler from startup_stm32f407xx.o(.text) referenced from startup_stm32f407xx.o(RESET)
- TIM2_IRQHandler from startup_stm32f407xx.o(.text) referenced from startup_stm32f407xx.o(RESET)
- TIM3_IRQHandler from startup_stm32f407xx.o(.text) referenced from startup_stm32f407xx.o(RESET)
- TIM4_IRQHandler from startup_stm32f407xx.o(.text) referenced from startup_stm32f407xx.o(RESET)
- TIM5_IRQHandler from startup_stm32f407xx.o(.text) referenced from startup_stm32f407xx.o(RESET)
- TIM6_DAC_IRQHandler from startup_stm32f407xx.o(.text) referenced from startup_stm32f407xx.o(RESET)
- TIM7_IRQHandler from startup_stm32f407xx.o(.text) referenced from startup_stm32f407xx.o(RESET)
- TIM8_BRK_TIM12_IRQHandler from startup_stm32f407xx.o(.text) referenced from startup_stm32f407xx.o(RESET)
- TIM8_CC_IRQHandler from startup_stm32f407xx.o(.text) referenced from startup_stm32f407xx.o(RESET)
- TIM8_TRG_COM_TIM14_IRQHandler from startup_stm32f407xx.o(.text) referenced from startup_stm32f407xx.o(RESET)
- TIM8_UP_TIM13_IRQHandler from startup_stm32f407xx.o(.text) referenced from startup_stm32f407xx.o(RESET)
- UART4_IRQHandler from startup_stm32f407xx.o(.text) referenced from startup_stm32f407xx.o(RESET)
- UART5_IRQHandler from startup_stm32f407xx.o(.text) referenced from startup_stm32f407xx.o(RESET)
- USART1_IRQHandler from startup_stm32f407xx.o(.text) referenced from startup_stm32f407xx.o(RESET)
- USART2_IRQHandler from startup_stm32f407xx.o(.text) referenced from startup_stm32f407xx.o(RESET)
- USART3_IRQHandler from startup_stm32f407xx.o(.text) referenced from startup_stm32f407xx.o(RESET)
- USART6_IRQHandler from startup_stm32f407xx.o(.text) referenced from startup_stm32f407xx.o(RESET)
- UsageFault_Handler from stm32f4xx_it.o(i.UsageFault_Handler) referenced from startup_stm32f407xx.o(RESET)
- WWDG_IRQHandler from startup_stm32f407xx.o(.text) referenced from startup_stm32f407xx.o(RESET)
- __main from entry.o(.ARM.Collect$$$$00000000) referenced from startup_stm32f407xx.o(.text)
- fputc from main.o(i.fputc) referenced from printf1.o(i.__0printf$1)
- main from main.o(i.main) referenced from entry9a.o(.ARM.Collect$$$$0000000B)

### Global Symbols

__main (Thumb, 0 bytes, Stack size unknown bytes, entry.o(.ARM.Collect$$$$00000000))
[Address Reference Count : 1]

- startup_stm32f407xx.o(.text)

_main_stk (Thumb, 0 bytes, Stack size unknown bytes, entry2.o(.ARM.Collect$$$$00000001))

_main_scatterload (Thumb, 0 bytes, Stack size unknown bytes, entry5.o(.ARM.Collect$$$$00000004))

[Calls]

- >> __scatterload

__main_after_scatterload (Thumb, 0 bytes, Stack size unknown bytes, entry5.o(.ARM.Collect$$$$00000004))

[Called By]

- >> __scatterload

_main_clock (Thumb, 0 bytes, Stack size unknown bytes, entry7b.o(.ARM.Collect$$$$00000008))

_main_cpp_init (Thumb, 0 bytes, Stack size unknown bytes, entry8b.o(.ARM.Collect$$$$0000000A))

_main_init (Thumb, 0 bytes, Stack size unknown bytes, entry9a.o(.ARM.Collect$$$$0000000B))

__rt_final_cpp (Thumb, 0 bytes, Stack size unknown bytes, entry10a.o(.ARM.Collect$$$$0000000D))

__rt_final_exit (Thumb, 0 bytes, Stack size unknown bytes, entry11a.o(.ARM.Collect$$$$0000000F))

Reset_Handler (Thumb, 8 bytes, Stack size 0 bytes, startup_stm32f407xx.o(.text))
[Address Reference Count : 1]

- startup_stm32f407xx.o(RESET)

ADC_IRQHandler (Thumb, 0 bytes, Stack size 0 bytes, startup_stm32f407xx.o(.text))

[Calls]

- >> ADC_IRQHandler

[Called By]

- >> ADC_IRQHandler

[Address Reference Count : 1]

- startup_stm32f407xx.o(RESET)

CAN1_RX0_IRQHandler (Thumb, 0 bytes, Stack size 0 bytes, startup_stm32f407xx.o(.text))
[Address Reference Count : 1]

- startup_stm32f407xx.o(RESET)

CAN1_RX1_IRQHandler (Thumb, 0 bytes, Stack size 0 bytes, startup_stm32f407xx.o(.text))
[Address Reference Count : 1]

- startup_stm32f407xx.o(RESET)

CAN1_SCE_IRQHandler (Thumb, 0 bytes, Stack size 0 bytes, startup_stm32f407xx.o(.text))
[Address Reference Count : 1]

- startup_stm32f407xx.o(RESET)

CAN1_TX_IRQHandler (Thumb, 0 bytes, Stack size 0 bytes, startup_stm32f407xx.o(.text))
[Address Reference Count : 1]

- startup_stm32f407xx.o(RESET)

CAN2_RX0_IRQHandler (Thumb, 0 bytes, Stack size 0 bytes, startup_stm32f407xx.o(.text))
[Address Reference Count : 1]

- startup_stm32f407xx.o(RESET)

CAN2_RX1_IRQHandler (Thumb, 0 bytes, Stack size 0 bytes, startup_stm32f407xx.o(.text))
[Address Reference Count : 1]

- startup_stm32f407xx.o(RESET)

CAN2_SCE_IRQHandler (Thumb, 0 bytes, Stack size 0 bytes, startup_stm32f407xx.o(.text))
[Address Reference Count : 1]

- startup_stm32f407xx.o(RESET)

CAN2_TX_IRQHandler (Thumb, 0 bytes, Stack size 0 bytes, startup_stm32f407xx.o(.text))
[Address Reference Count : 1]

- startup_stm32f407xx.o(RESET)

DCMI_IRQHandler (Thumb, 0 bytes, Stack size 0 bytes, startup_stm32f407xx.o(.text))
[Address Reference Count : 1]

- startup_stm32f407xx.o(RESET)

DMA1_Stream0_IRQHandler (Thumb, 0 bytes, Stack size 0 bytes, startup_stm32f407xx.o(.text))
[Address Reference Count : 1]

- startup_stm32f407xx.o(RESET)

DMA1_Stream1_IRQHandler (Thumb, 0 bytes, Stack size 0 bytes, startup_stm32f407xx.o(.text))
[Address Reference Count : 1]

- startup_stm32f407xx.o(RESET)

DMA1_Stream2_IRQHandler (Thumb, 0 bytes, Stack size 0 bytes, startup_stm32f407xx.o(.text))
[Address Reference Count : 1]

- startup_stm32f407xx.o(RESET)

DMA1_Stream3_IRQHandler (Thumb, 0 bytes, Stack size 0 bytes, startup_stm32f407xx.o(.text))
[Address Reference Count : 1]

- startup_stm32f407xx.o(RESET)

DMA1_Stream4_IRQHandler (Thumb, 0 bytes, Stack size 0 bytes, startup_stm32f407xx.o(.text))
[Address Reference Count : 1]

- startup_stm32f407xx.o(RESET)

DMA1_Stream5_IRQHandler (Thumb, 0 bytes, Stack size 0 bytes, startup_stm32f407xx.o(.text))
[Address Reference Count : 1]

- startup_stm32f407xx.o(RESET)

DMA1_Stream6_IRQHandler (Thumb, 0 bytes, Stack size 0 bytes, startup_stm32f407xx.o(.text))
[Address Reference Count : 1]

- startup_stm32f407xx.o(RESET)

DMA1_Stream7_IRQHandler (Thumb, 0 bytes, Stack size 0 bytes, startup_stm32f407xx.o(.text))
[Address Reference Count : 1]

- startup_stm32f407xx.o(RESET)

DMA2_Stream0_IRQHandler (Thumb, 0 bytes, Stack size 0 bytes, startup_stm32f407xx.o(.text))
[Address Reference Count : 1]

- startup_stm32f407xx.o(RESET)

DMA2_Stream1_IRQHandler (Thumb, 0 bytes, Stack size 0 bytes, startup_stm32f407xx.o(.text))
[Address Reference Count : 1]

- startup_stm32f407xx.o(RESET)

DMA2_Stream2_IRQHandler (Thumb, 0 bytes, Stack size 0 bytes, startup_stm32f407xx.o(.text))
[Address Reference Count : 1]

- startup_stm32f407xx.o(RESET)

DMA2_Stream3_IRQHandler (Thumb, 0 bytes, Stack size 0 bytes, startup_stm32f407xx.o(.text))
[Address Reference Count : 1]

- startup_stm32f407xx.o(RESET)

DMA2_Stream4_IRQHandler (Thumb, 0 bytes, Stack size 0 bytes, startup_stm32f407xx.o(.text))
[Address Reference Count : 1]

- startup_stm32f407xx.o(RESET)

DMA2_Stream5_IRQHandler (Thumb, 0 bytes, Stack size 0 bytes, startup_stm32f407xx.o(.text))
[Address Reference Count : 1]

- startup_stm32f407xx.o(RESET)

DMA2_Stream6_IRQHandler (Thumb, 0 bytes, Stack size 0 bytes, startup_stm32f407xx.o(.text))
[Address Reference Count : 1]

- startup_stm32f407xx.o(RESET)

DMA2_Stream7_IRQHandler (Thumb, 0 bytes, Stack size 0 bytes, startup_stm32f407xx.o(.text))
[Address Reference Count : 1]

- startup_stm32f407xx.o(RESET)

ETH_IRQHandler (Thumb, 0 bytes, Stack size 0 bytes, startup_stm32f407xx.o(.text))
[Address Reference Count : 1]

- startup_stm32f407xx.o(RESET)

ETH_WKUP_IRQHandler (Thumb, 0 bytes, Stack size 0 bytes, startup_stm32f407xx.o(.text))
[Address Reference Count : 1]

- startup_stm32f407xx.o(RESET)

EXTI0_IRQHandler (Thumb, 0 bytes, Stack size 0 bytes, startup_stm32f407xx.o(.text))
[Address Reference Count : 1]

- startup_stm32f407xx.o(RESET)

EXTI15_10_IRQHandler (Thumb, 0 bytes, Stack size 0 bytes, startup_stm32f407xx.o(.text))
[Address Reference Count : 1]

- startup_stm32f407xx.o(RESET)

EXTI1_IRQHandler (Thumb, 0 bytes, Stack size 0 bytes, startup_stm32f407xx.o(.text))
[Address Reference Count : 1]
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

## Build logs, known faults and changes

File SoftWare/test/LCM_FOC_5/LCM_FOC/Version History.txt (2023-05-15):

/******************** (C) COPYRIGHT 2020 LCM MotorControl Lab
*Update History
 ******************************************************************************
* File Name         	: Version History.txt
* Author             	: LCM MotorControl Team
* Version            	: V2.1
* Date               	: 11/26/2021
* Description        	: 1)update sdk to v1.0.7；
		  2)add ACMP_BRK Block
*******************************************************************************/
 ******************************************************************************
* File Name	: Version History.txt
* Author             	: LCM MotorControl Team
* Version            	: V3.2
* Date               	: 12/29/2021
* Description        	: 1)add Idc measurement
	             	  2)add hardware overcurrent protection
*******************************************************************************/

******************* (C) COPYRIGHT 2020 LCM MotorControl Lab ********************
20221011  增加上电检测
20221021  MTPA
20230325  GPIO 修改，硬件版本修改

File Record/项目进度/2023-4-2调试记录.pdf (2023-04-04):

转速 RPM | 电流 A
1000 | 0.69
1400 | 1.4
1600 | 1.9
1800 | 2.5
2200 | 4.05
2400 | 5.0
2600 | 6.2
2800 | 7.6
3000 | 9.3
3200 | 11
3400 | 13.16
3600 | 13.6
3700 | 13.6
3800 | 13.6

# 2023-4-2调试记录

# PMSM 48V 带负载测试

# 测试总结

3700RPM后转速无明显提升，电流无明显提升。

# 后续工作

排查转速原因

修复数码管显示问题(驱动代码无异常，疑似硬件问题。)

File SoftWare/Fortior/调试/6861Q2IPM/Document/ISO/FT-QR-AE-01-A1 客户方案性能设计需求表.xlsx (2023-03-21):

 |  |  |  |  |  |  |  |  | 表单编号： | FT-QR-AE-01-A1
 |  |  |  |  |  |  |  |  | REG#: | R10003451
客户方案性能设计需求表
一、方案来源
客户名称： |  | 新科 |  |  | 方案名称： | 空调压缩机 |  | 方案应用： | 空调
客户工程师： |  | 刘工 |  |  | 联系电话： | 18998012287 |  | 邮 箱：
二、产品电机参数
序号 | 项目 |  |  | 参数 |  | 序号 | 项目 |  | 参数
1 | 相电阻(Ω) |  |  |  |  | 2 | 相电感 Ld,Lq(mH)
3 | 极对数（个） |  |  |  |  | 4 | 感应电动势常数Ke(V/Krpm)
5 | 有无HALL |  |  | □有Hall □无Hall |  | 6 | HALL个数
7 | HALL与B-EMF关系 |  |  | □超前 □重合 □滞后 |  | 8 | HALL类型 |  | □Hall Sensor □Hall IC
三、产品基本性能设计需求
序号 | 设计需求 |  |  | 设计指标
1 | 工作电压（V） |  |  | 最小值：180v 额定值： 220v 最大值： 250v
2 | 工作电流范围（A） |  |  | 0-10A
3 | 输入功率范围（W） |  |  | 1800W
4 | 空载转速（RPM）
5 | 带载转速范围（RPM）
6 | 控制方式 |  |  | □方波120° □150° □正弦波 ■FOC
7 | 启动参数 | 模式选择 |  | □软启动 □快速启动 ■正常启动
 |  | 启动时间
8 | 正反转 | 是否需要 |  | □是 ■否
 |  | 反转等待时间
9 | 调速 | 是 | 模拟调速 | 调速范围：
 |  |  |  | 电压范围：
 |  |  | 数字调试 | 调速范围：
 |  |  |  | Duty范围：
 |  |  |  | PWM频率范围：
 |  | 否
10 | 开、闭环模式 |  |  | ■开环 □闭环(目标转速： )
11 | 刹车功能 |  |  | 刹车速度：
12 | 堵转功能 |  |  | ■需要 | 堵转检测时间： | 50ms |  | 堵转重启时间： | 2s
 |  |  |  | □不需要
13 | 限流功能 |  |  | □需要 | 限流大小：
 |  |  |  | ■不需要
14 | 过压保护功能 |  |  | ■需要 | 过压保护值： | 380V |  | 过压保护恢复值： | 320V
 |  |  |  | □不需要
15 | 过流保护功能 |  |  | ■需要 | 过流保护值： | 20A
 |  |  |  | □不需要
16 | 欠电压保护 |  |  | ■需要 | 欠电压保护值： | 120V
 |  |  |  | □不需要
17 | 缺相保护 |  |  | ■需要
 |  |  |  | □不需要
18 | 噪音要求 |  |  | ≤ DB
19 | ESD要求
20 | EMC要求
21 | 工作环境温度要求
22 | 热拔插
23 | 成本
24 | 开发周期
四、备注
 | 应用部确认： |  |  |  | 市场部确认：
 | 日期： |  |  |  | 日期：

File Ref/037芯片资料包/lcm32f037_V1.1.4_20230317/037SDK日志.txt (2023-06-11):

1.0.5：重新整理SDK初版

1.0.6：优化OPA校准忽略ANA寄存器问题；
           优化SYSTICK延时未保存客户配置问题；
           优化ADC配置寄存器 1 (ADC_CFGR1)bit4:3 FIFO配置部分未增加导致开通ADC通道过多时，bit2和bit5置位被改变。
           优化DMA触发源通道库定义错误问题；
          重新整理了037大部分外设功能的demo；

1.0.7：实测chipctrl寄存器写入时解锁一次仅可修改一次；而库函数有些部分解锁一次连续写入两次，导致第二次写入失败，库已修改
          新增外部中断demo
          新增TIM15捕获ACMP0_OUT的demo
          新增OPA_NIN引脚库函数；
          新增软件IIC的demo；

1.0.7：忘记添加TIM_TI3E_Set和TIM_TI4E_Set库函数，已增加；
         补全ADC时钟PLL分频；
         修改.h文件；
         ADC通道16、17库宏定义写反了；
         优化IIC库并给出demo；

1.0.8 优化外部中断不能多引脚同时配置问题，库已修改
        增加主频切换程序（20211206）
        新增TIM1_CH4的PWM输出比较中断（20211213）
        修改模拟EEPROM例程（1215曾）
        优化操作信息区例程（1215曾）
        新增复位脚作为普通IO配置库函数（1220）
        优化串口收发程序（1220）
       优化ADC_ChannelConfig通道选择库函数（1223）
       重写IIC的库以及例程（20220117）
       新增LVD_LVR例程（0119）
       新增ACMP_HALLMID例程（0119）
      优化DMA库函数，新增TIM1通过DMA 将CCR1搬运到CCR3（0119）
      优化GPIO强驱配置库函数并新增例程（0119）

1.0.9新增TIM16/17例程（0124）
       新增ADC模拟看门狗例程，优化ADC模拟看门狗部分库函数（0125）
       优化GPIO输出模式与上下拉没有硬件约束导致配置中容易增加功耗（0214）
       实测发现ADC触发中边沿模式比"电平"模式更容易丢触发；库默认改为“电平”模式（0215）
       新增TIM1捕获ACMP0 output；（0215）
       新增TIM1捕获ACMP1 output；（0215）
       新增TIM1捕获ACMP2 output；（0215）
       新增TIM1捕获TIM15_OC1；（0215）
       新增TIM1捕获TIM3_OC1；（0215）
       新增TIM1捕获TIM14_OC1；（0215）
       新增TIM3捕获ACMP0 output；（0215）
       新增TIM3捕获ACMP1 output；（0215）
       新增TIM3捕获ACMP2 output；（0215）
       新增TIM3捕获TIM1_OC1；（0215）
       新增TIM3捕获TIM15_OC1；（0215）
       新增TIM3捕获TIM16_OC1；（0215）
       新增TIM15捕获ACMP0 output；（0215）
       新增TIM15捕获ACMP1 output；（0215）
       新增TIM15捕获ACMP2 output；（0215）
       新增TIM15捕获TIM1_OC1；（0215）
       新增TIM15捕获TIM3_OC1；（0215）
       新增TIM15捕获TIM14_OC1；（0215）
       修改TIM_ClearITPendingBit库函数错误项（0523）
       新增SSP0，SSP2,SSP0_DMA例程,（0601）
       优化WT例程和库(0601)
1.1.0 更改8M和16M库函数（0613）
        优化DMA库函数（0615）
1.1.1 M0内核中断优先级个数配置错误，已修改（0708）
         优化ADC_ChannelConfig函数（0714）
         修改库函数高频配置，增加高频配置例程（0728）
        TIM1新增死区例程（0728）
1.1.2把主频配置移出SystemInit，新增函数SetSysClock配置主频，并优化PLL配置（0809）
       新增ADC_GetVTStemperature函数，返回值为温度（0809）
      新增切换VTS通道例程（0809）
1.1.3新增CRC库及例程（0818）
        新增TIM3编码器例程
        新增SSP2的主机DMA发送例程（1013）
        更新DMA优先级等级（1101）
        新增在hardfault中断服务程序中增加软复位调用（1115）
         IWDG例程新增配置完成等待标志（1213）
         纠正OB_BASE基地址（1216）
        新增TIM14捕获例程（1228）
        优化GPIO初始化上下拉配置，解决上下拉配置来回切换问题（0105）
        优化GPIO强驱不能多次配置问题（0105）
       优化模拟EEPROM例程，之前例程不完整会导致换页丢失数据（0215）
       TIM1新增LVD刹车例程（0216）
       OPA初始化漏写VM_SEL位配置（0224）

1.1.4系统延时去掉中断使能（0310）
       宏定义UART_STATUS_nCTS与其他定义不匹配，修改为UART_STATUS_CTS统一格式（0315）
       去掉RCC_APB0Periph_TIM16错误宏定义（0317）

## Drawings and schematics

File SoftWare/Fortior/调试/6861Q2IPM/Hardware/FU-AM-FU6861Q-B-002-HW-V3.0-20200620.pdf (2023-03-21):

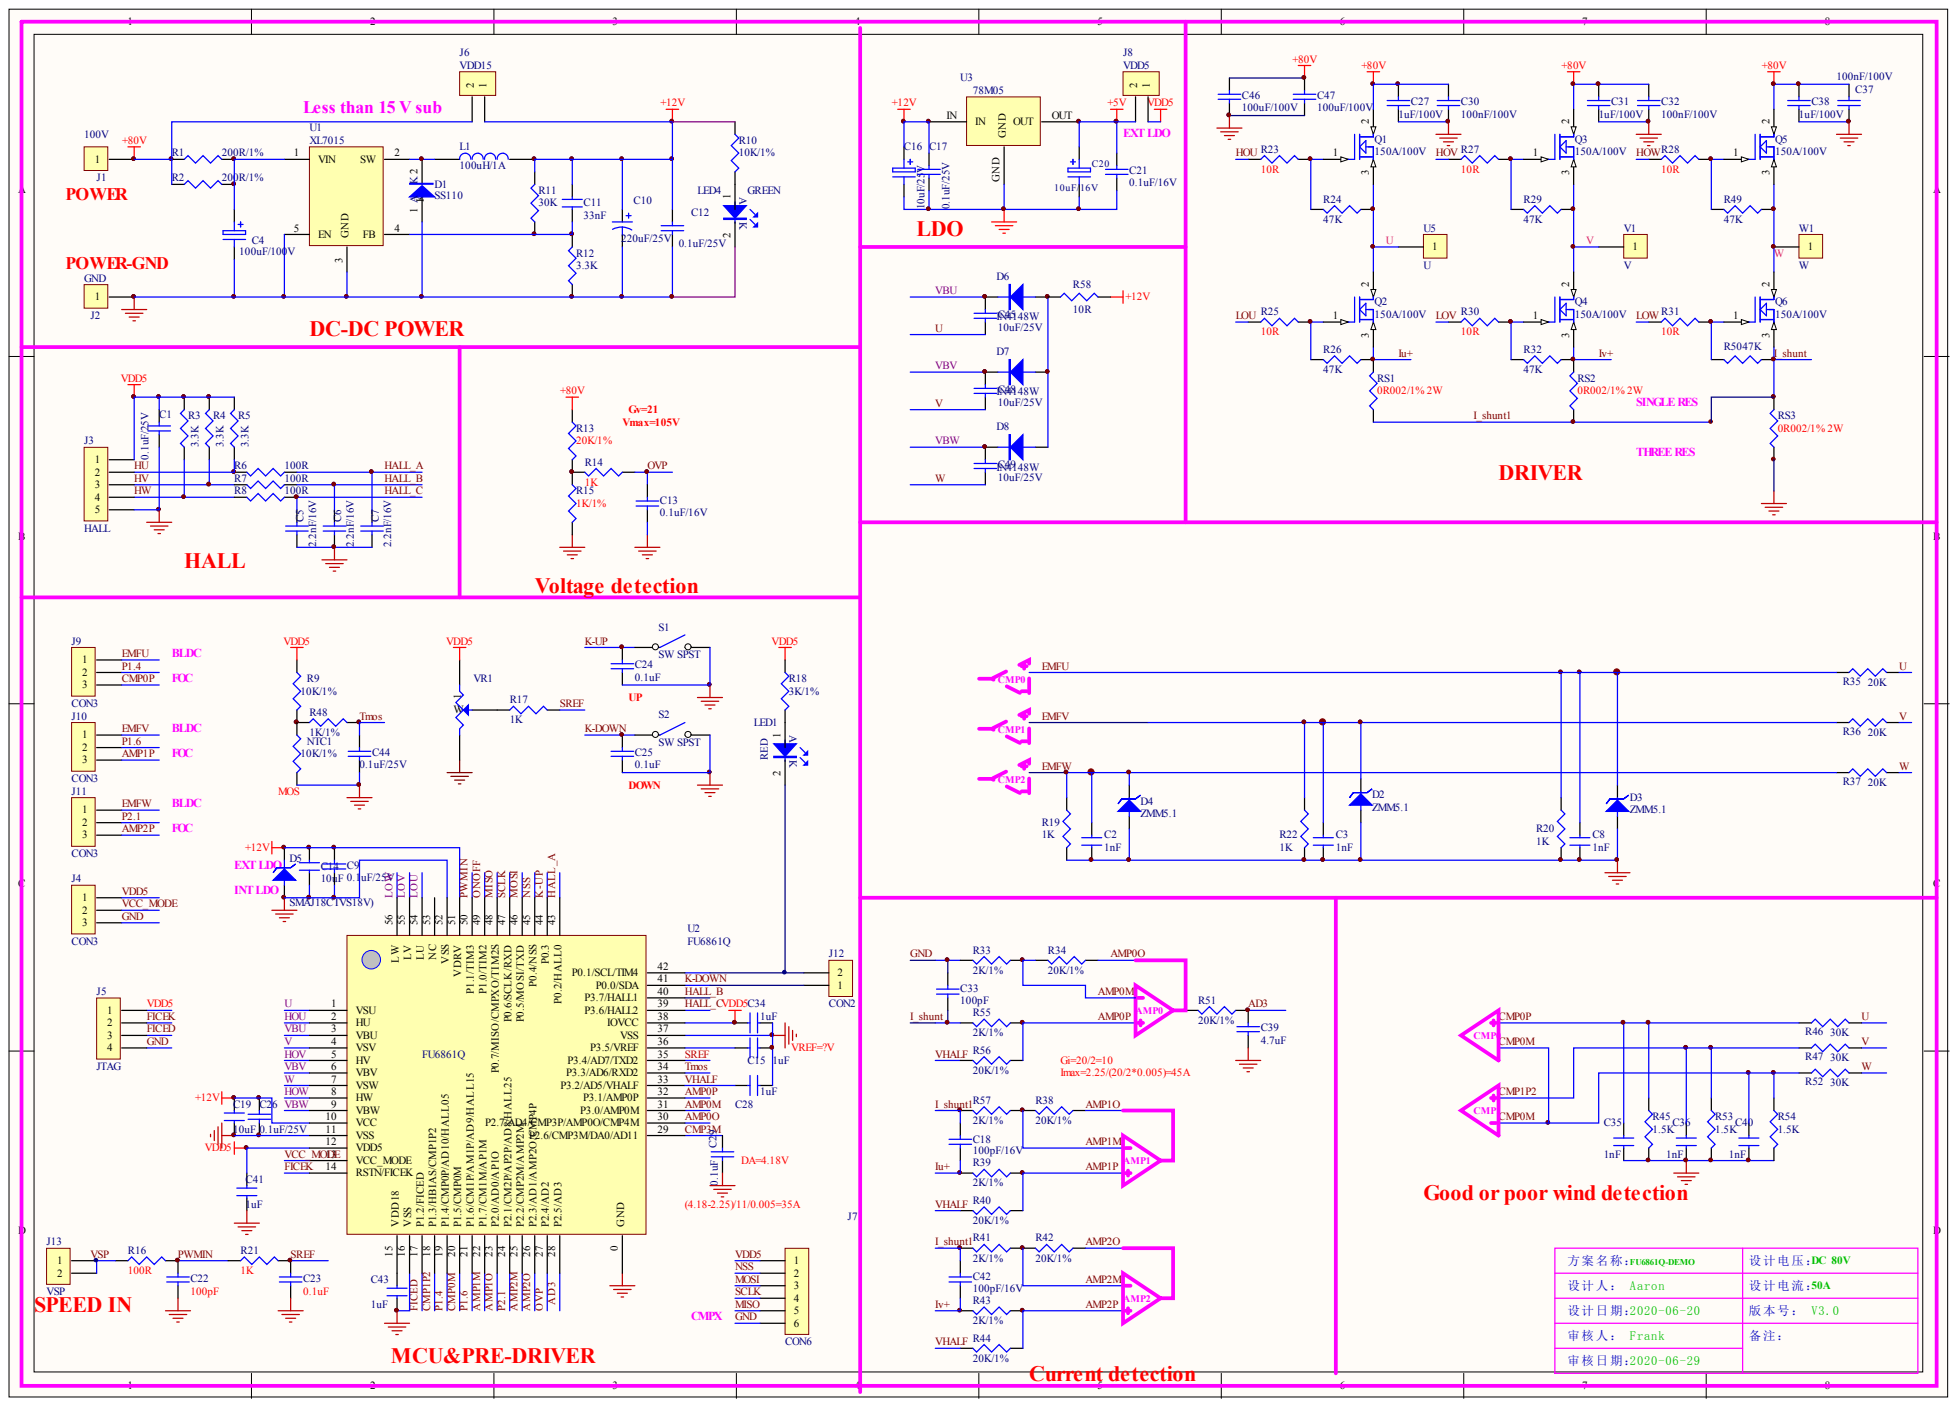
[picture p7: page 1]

HU
HV | R7 100R | HALL_B

VDRV 51 VSS 52 NC 53 LU 54 LV 55 LW 56

P0.2/HALL0 43 P0.3 44 P0.4/NSS 45 P0.5/MOSI/TXD 46 P0.6/SCLK/RXD 47 P0.7/MISO/CMPXO/TIM2S 48 P1.0/TIM2 49 P1.1/TIM3 50

10uF | 0.1uF/25V | VSS 11 | CMP3M

VDD5 12

Good or poor wind detection

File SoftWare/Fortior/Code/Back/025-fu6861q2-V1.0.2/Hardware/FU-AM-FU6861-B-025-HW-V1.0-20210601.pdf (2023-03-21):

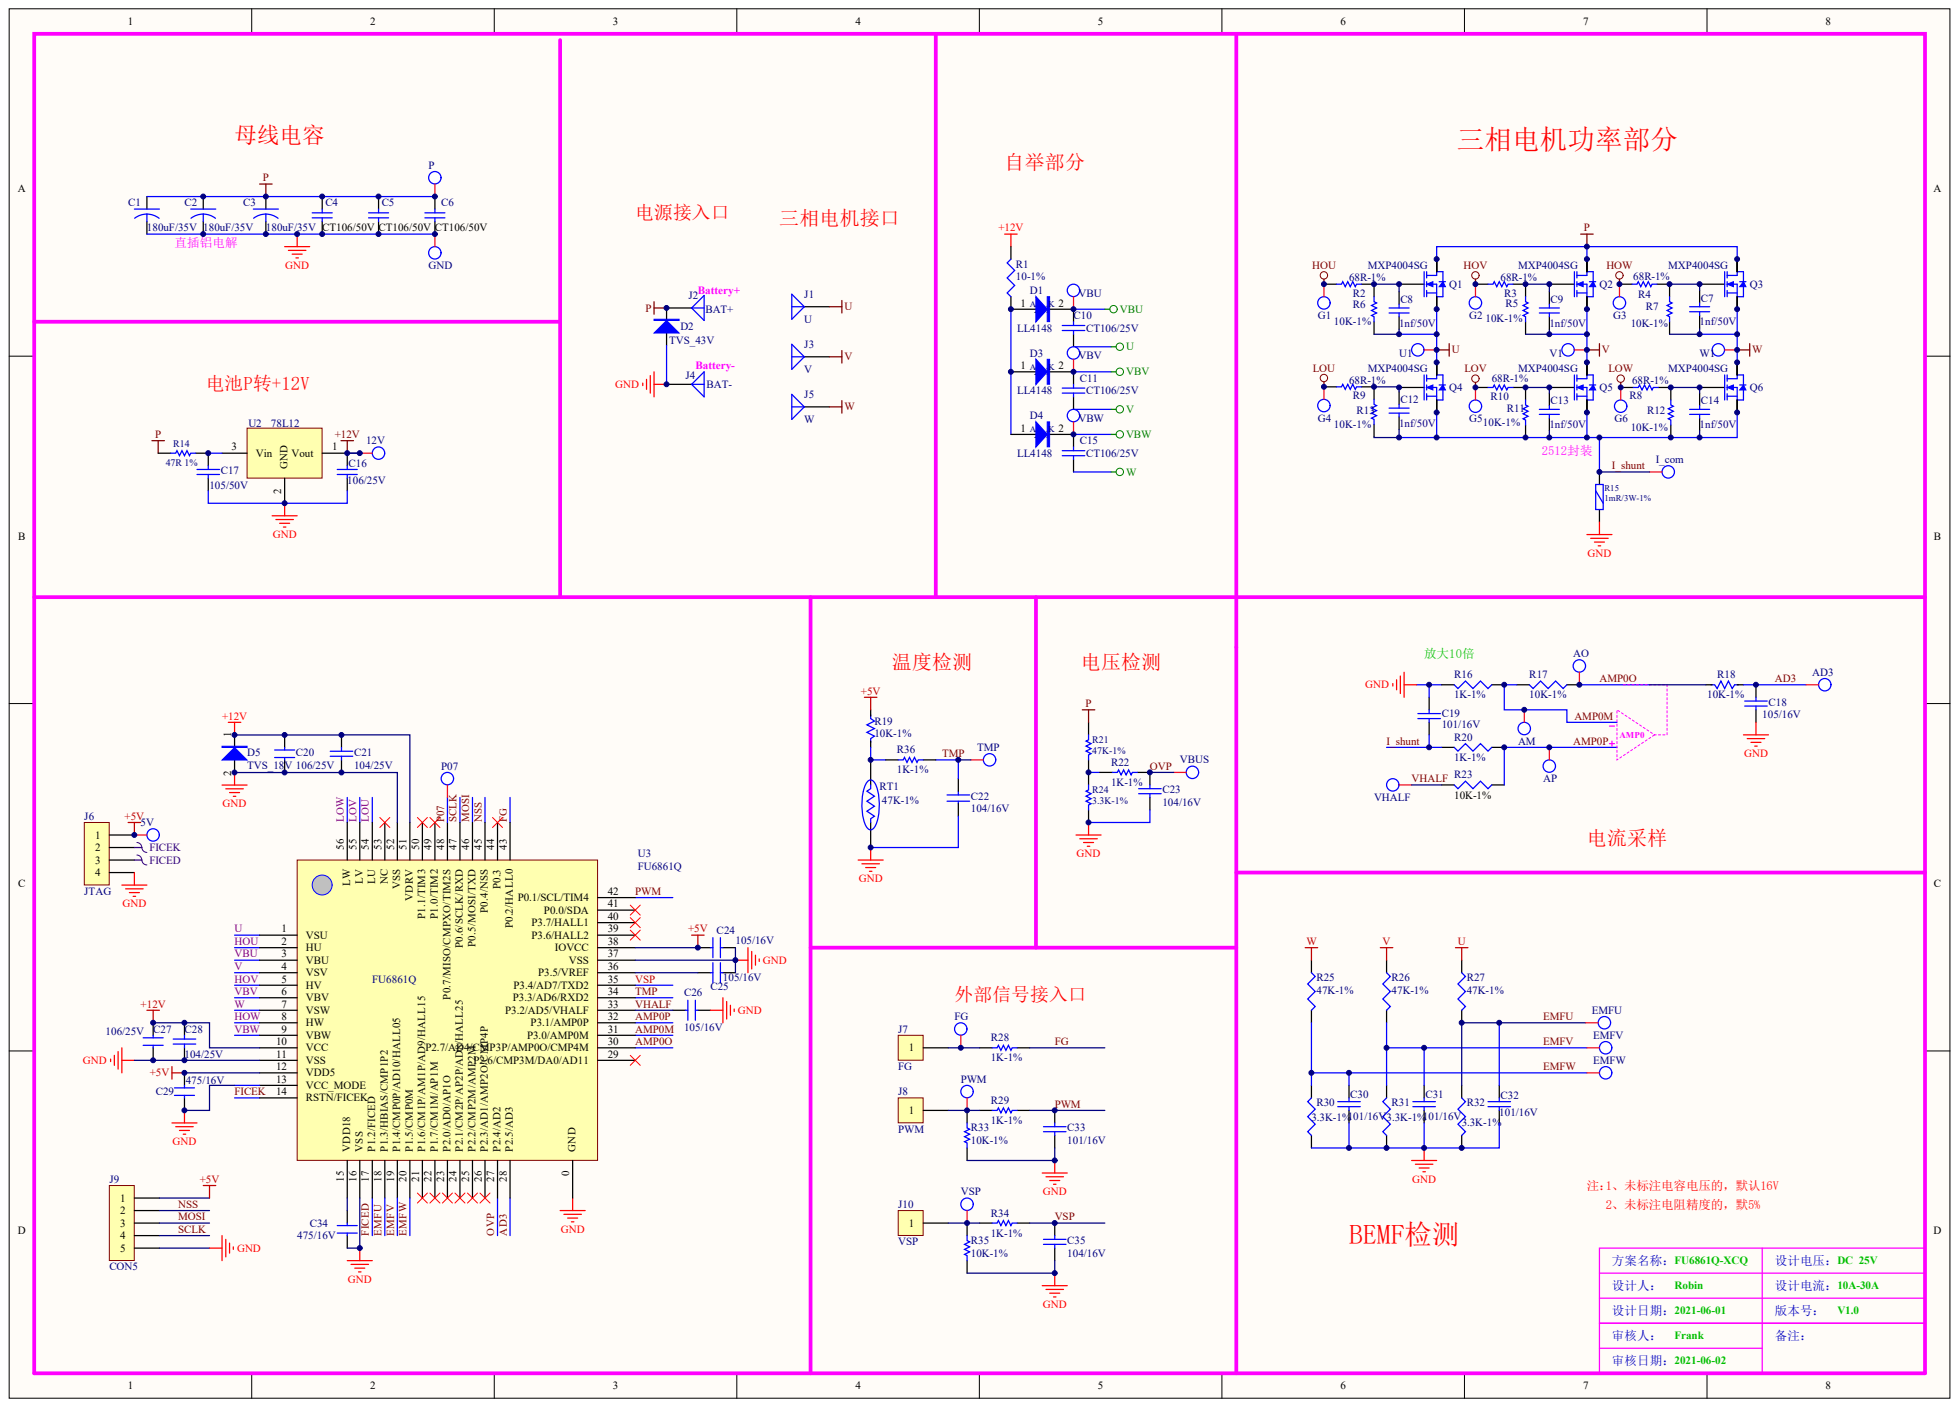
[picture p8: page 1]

VDRV 51 VSS 52 NC 53 LU 54 LV 55 LW 56

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

方案名称：FU6861Q-XCQ | 设计电压： DC 25V

设计人： Robin | 设计电流： 10A-30A

设计日期： 2021-06-01 | 版本号： V1.0

审核人： Frank

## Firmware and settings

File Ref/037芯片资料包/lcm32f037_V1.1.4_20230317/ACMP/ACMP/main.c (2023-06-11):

#include "lcm32f037_conf.h"
#include "lcm32f037.h"
#include "lcm32f037_rcc.h"
#include "lcm32f037_uart.h"
#include "lcm32f037_gpio.h"
#include <stdio.h>
#include <stdlib.h>
#include <string.h>
#include "lcm32f037_div.h"
#include "lcm32f037_tim.h"
#include "lcm32f037_acmp.h"
#include "lcm32f037_dac.h"
#include "lcm32f037_exti.h"
#include "lcm32f037_dma.h"
/**************************
3路比较器:I/O 端口、HALL、DAC 和比较器之间可实现互联；


demo为 ACMP0单通道比较，可不需要触发；
		ACMP1为多通道连续比较，软件触发；软件触发需要START，且START一次仅转换一个序列；
		ACMP2为多通道比较，硬件触发；硬件触发不需要配置START

连续模式必须要触发，连续模式若选择软件触发，
则每次START(调用函数SATRT_OFACMP0/1/2();)仅转换一个序列

主频16M，硬件触发连续模式建议不超过1.5K；主频提高，硬件触发频率也可以随之增加
***************************************/

/******************************
ACMP0配置为正端IO输入，负端为DAC0;单通道比较，非连续
************************************************************************/
void delay(uint32_t dly)
{
	volatile uint32_t i = 0;
	while (i++ < dly)
		;
}

void DAC0_cfg()
{
	GPIO_InitTypeDef GPIO_InitStruct;
	GPIO_InitStruct.GPIO_Pin = GPIO_Pin_10;
	GPIO_InitStruct.GPIO_Mode = GPIO_Mode_AN;
	GPIO_InitStruct.GPIO_Speed = GPIO_Speed_Level_2;
	GPIO_InitStruct.GPIO_OType = GPIO_OType_PP;
	GPIO_InitStruct.GPIO_PuPd = GPIO_PuPd_NOPULL;
	GPIO_Init(GPIOA, &GPIO_InitStruct);
	GPIO_PinAFConfig(GPIOA, GPIO_PinSource10, GPIO_AF_2); //用于观测DAC0_OUT

	DAC_InitTypeDef DAC_InitStruct;
	DAC_InitStruct.DAC_Trigger_Source = DAC_Trigger_Software;
	DAC_InitStruct.DAC_WaveGeneration = DAC_WaveGeneration_None;
	DAC_InitStruct.DAC_LFSRUnmask_TriangleAmplitude = DAC_LFSRUnmask_Bit0;
	DAC_InitStruct.DAC_OutputBuffer = DAC0_OutputBuffer_Enable;
	DAC_InitStruct.DAC_Vref_Select = DAC_Vref_Avdd;
	DAC_InitStruct.DAC_EXTrigger_Edge = DAC_EXTrigger_edge_dis;
	DAC_InitStruct.DAC_DmaMode = DISABLE;
	DAC_InitStruct.DAC_DMAUDR_IE = DISABLE;
	DAC_Init(DAC0, &DAC_InitStruct);

	DAC_Cmd(DAC0, ENABLE);
	DAC_SetDac_10B_Data(DAC0, DAC_Align_10B_R, 0x1FF);
	DAC_SoftwareTriggerCmd(DAC0, ENABLE); //软件触发使能；标示触发 DAC 的一次触发传输(选择软件触发条件)
}
void acmp0_cfg()
{
	GPIO_InitTypeDef GPIO_InitStructure;

	GPIO_InitStructure.GPIO_Pin = GPIO_Pin_0;
	GPIO_InitStructure.GPIO_Mode = GPIO_Mode_AF;
	GPIO_InitStructure.GPIO_Speed = GPIO_Speed_Level_2;
	GPIO_InitStructure.GPIO_OType = GPIO_OType_PP;
	GPIO_Init(GPIOA, &GPIO_InitStructure);
	GPIO_PinAFConfig(GPIOA, GPIO_PinSource0, GPIO_AF_6); ////out

	GPIO_InitStructure.GPIO_Pin = GPIO_Pin_1;
	GPIO_InitStructure.GPIO_Mode = GPIO_Mode_AN;
	GPIO_InitStructure.GPIO_Speed = GPIO_Speed_Level_2;
	GPIO_InitStructure.GPIO_OType = GPIO_OType_PP;
	GPIO_Init(GPIOA, &GPIO_InitStructure);
	GPIO_PinAFConfig(GPIOA, GPIO_PinSource1, GPIO_AF_2); // CP0_P_1[1]

	GPIO_InitStructure.GPIO_Pin = GPIO_Pin_0;
	GPIO_InitStructure.GPIO_Mode = GPIO_Mode_AN;
	GPIO_InitStructure.GPIO_Speed = GPIO_Speed_Level_2;
	GPIO_InitStructure.GPIO_OType = GPIO_OType_PP;
	GPIO_Init(GPIOF, &GPIO_InitStructure);
	GPIO_PinAFConfig(GPIOF, GPIO_PinSource0, GPIO_AF_1); ////CP0_N_3[2]

	ACMP_InitTypeDef ACMP_InitStruct;
	ACMP_InitStruct.ACMP_P_Select = CP0_PS_CPP0EXT_INPUT; //比较器正端输入选择
	ACMP_InitStruct.ACMP_N_Select = CP0_NS_DAC0OUT;		  //比较器负端输入选择
	ACMP_InitStruct.ACMP_Delay_time = CP_NODelay_time;	  //输出延迟配置
	ACMP_InitStruct.ACMP_Blanking = CP_NOBLANKING;		  //比较器消隐源选择
	ACMP_InitStruct.ACMP_Is = CP_IS_POS;				  //比较器输出极性
	ACMP_InitStruct.ACMP_HYSEN = DISABLE;				  //迟滞使能配置
	ACMP_InitStruct.ACMP_FREN = ENABLE;					  //快速响应使能
	ACMP_InitStruct.ACMP_FS = DISABLE;					  //输出滤波使能配置

	ACMP_InitStruct.CMP_INTENMASK = ENABLE;				 //比较器连续比较中断使能屏蔽
	ACMP_InitStruct.CMP_SEQ_MODE = DISABLE;				 //连续模式使能
	ACMP_InitStruct.TRIG_MODE = CP_TIRG_INASOFT;		 //触发模式：软件或者外部硬件触发
	ACMP_InitStruct.CHNL_CNT_TIME = CHNL_CNT_TIME_64CLK; //比较器通道切换时钟周期选择

	ACMP0_Init(&ACMP_InitStruct);
	ACMP0_SEQ_INPUT_SELECT(DISABLE, 5, 2); //选择输入通道：是否连续；正端；负端
	ACMP0_Cmd(ENABLE);
}

/******************************
ACMP1为连续比较模式，软件触发，需要START
************************************************************************/
void acmp1_cfg()
{
	GPIO_InitTypeDef GPIO_InitStructure;

	GPIO_InitStructure.GPIO_Pin = GPIO_Pin_2;
	GPIO_InitStructure.GPIO_Mode = GPIO_Mode_AF;
	GPIO_InitStructure.GPIO_Speed = GPIO_Speed_Level_2;
	GPIO_InitStructure.GPIO_OType = GPIO_OType_PP;
	GPIO_Init(GPIOA, &GPIO_InitStructure);
	GPIO_PinAFConfig(GPIOA, GPIO_PinSource2, GPIO_AF_6); ////out

	GPIO_InitStructure.GPIO_Pin = GPIO_Pin_1;
	GPIO_InitStructure.GPIO_Mode = GPIO_Mode_AN;
	GPIO_InitStructure.GPIO_Speed = GPIO_Speed_Level_2;
	GPIO_InitStructure.GPIO_OType = GPIO_OType_PP;
	GPIO_Init(GPIOF, &GPIO_InitStructure);
	GPIO_PinAFConfig(GPIOF, GPIO_PinSource1, GPIO_AF_1); // CP1_P_P01[0]

	GPIO_InitStructure.GPIO_Pin = GPIO_Pin_3;
	GPIO_InitStructure.GPIO_Mode = GPIO_Mode_AN;
	GPIO_InitStructure.GPIO_Speed = GPIO_Speed_Level_2;
	GPIO_InitStructure.GPIO_OType = GPIO_OType_PP;
	GPIO_Init(GPIOA, &GPIO_InitStructure);
	GPIO_PinAFConfig(GPIOA, GPIO_PinSource3, GPIO_AF_1); // CP1_P_4[1]

	GPIO_InitStructure.GPIO_Pin = GPIO_Pin_7;
	GPIO_InitStructure.GPIO_Mode = GPIO_Mode_AN;
	GPIO_InitStructure.GPIO_Speed = GPIO_Speed_Level_2;
	GPIO_InitStructure.GPIO_OType = GPIO_OType_PP;
	GPIO_Init(GPIOF, &GPIO_InitStructure);
	GPIO_PinAFConfig(GPIOF, GPIO_PinSource7, GPIO_AF_2); ////CP1_N_5[2]

	ACMP_InitTypeDef ACMP_InitStruct;
	ACMP_InitStruct.ACMP_P_Select = CP1_PS_CPP1EXT_INPUT; //比较器正端输入选择
	ACMP_InitStruct.ACMP_N_Select = CP1_NS_CPN1EXT_INPUT; //比较器负端输入选择
	ACMP_InitStruct.ACMP_Delay_time = CP_NODelay_time;	  //输出延迟配置
	ACMP_InitStruct.ACMP_Blanking = CP_NOBLANKING;		  //比较器消隐源选择
	ACMP_InitStruct.ACMP_Is = CP_IS_POS;				  //比较器输出极性
	ACMP_InitStruct.ACMP_HYSEN = DISABLE;				  //迟滞使能配置
	ACMP_InitStruct.ACMP_FREN = ENABLE;					  //快速响应使能
	ACMP_InitStruct.ACMP_FS = DISABLE;					  //输出滤波使能配置

	ACMP_InitStruct.CMP_INTENMASK = ENABLE;				 //比较器连续比较中断使能屏蔽
	ACMP_InitStruct.CMP_SEQ_MODE = ENABLE;				 //连续模式使能
	ACMP_InitStruct.TRIG_MODE = CP_TIRG_INASOFT;		 //触发模式：软件或者外部硬件触发
	ACMP_InitStruct.CHNL_CNT_TIME = CHNL_CNT_TIME_64CLK; //比较器通道切换时钟周期选择

	ACMP1_Init(&ACMP_InitStruct);

	ACMP1_SEQ_INPUT_SELECT(ENABLE, 18, 2);

	ACMP1_Cmd(ENABLE);
}
/******************
ACMP1为连续比较模式，硬件触发，不需要START
主频16M，硬件触发连续模式建议不超过1.5K；主频提高，硬件触发频率也可以随之增加
*****************************************/
void tim1_cfg_init()
{
	TIM_TimeBaseInitTypeDef TIM_TimeBaseStructure;
	TIM_OCInitTypeDef TIM_OCInitStructure;

	uint16_t TimerPeriod = 0;
	uint16_t Channel1Pulse = 0, Channel2Pulse = 0, Channel3Pulse = 0, Channel4Pulse = 0;
	TimerPeriod = 16000; // 16000000/16000;
	Channel1Pulse = TimerPeriod / 2;

	/* Time Base configuration */
	TIM_TimeBaseStructure.TIM_Prescaler = 0;
	TIM_TimeBaseStructure.TIM_CounterMode = TIM_CounterMode_Up;
	TIM_TimeBaseStructure.TIM_Period = TimerPeriod;
	TIM_TimeBaseStructure.TIM_ClockDivision = 0;
	TIM_TimeBaseStructure.TIM_RepetitionCounter = 0;
	TIM_TimeBaseInit(TIM1, &TIM_TimeBaseStructure);

	/* Channel 1, 2,3 and 4 Configuration in PWM mode */
	TIM_OCInitStructure.TIM_OCMode = TIM_OCMode_PWM1;
	TIM_OCInitStructure.TIM_OutputState = TIM_OutputState_Enable;
	TIM_OCInitStructure.TIM_OutputNState = TIM_OutputNState_Enable;
	TIM_OCInitStructure.TIM_Pulse = Channel1Pulse;
	TIM_OCInitStructure.TIM_OCPolarity = TIM_OCPolarity_Low;
	TIM_OCInitStructure.TIM_OCNPolarity = TIM_OCNPolarity_High;
	TIM_OCInitStructure.TIM_OCIdleState = TIM_OCIdleState_Set;
	TIM_OCInitStructure.TIM_OCNIdleState = TIM_OCNIdleState_Reset;

	TIM_OC1Init(TIM1, &TIM_OCInitStructure);
	TIM_OC2Init(TIM1, &TIM_OCInitStructure);
	TIM_OC3Init(TIM1, &TIM_OCInitStructure);
	TIM_OC4Init(TIM1, &TIM_OCInitStructure);

	/* Enables the TIM1 Preload on CC1,CC2,CC3,CC4 Register */
	TIM_OC1PreloadConfig(TIM1, TIM_OCPreload_Enable);
	TIM_OC2PreloadConfig(TIM1, TIM_OCPreload_Enable);
	TIM_OC3PreloadConfig(TIM1, TIM_OCPreload_Enable);
	TIM_OC4PreloadConfig(TIM1, TIM_OCPreload_Enable);

	TIM_CtrlPWMOutputs(TIM1, ENABLE); //配置TRGO触发ADC可不需要使能，配置通道CCx触发,或通过IO观测PWM波形，必须使能；

	TIM_Cmd(TIM1, ENABLE);

	GPIO_InitTypeDef GPIO_InitStructure;
	//配置管脚为复用模式
	GPIO_InitStructure.GPIO_Pin = GPIO_Pin_8;
	GPIO_InitStructure.GPIO_Mode = GPIO_Mode_AF;
	GPIO_InitStructure.GPIO_Speed = GPIO_Speed_Level_2;
	GPIO_InitStructure.GPIO_OType = GPIO_OType_PP;
	GPIO_InitStructure.GPIO_PuPd = GPIO_PuPd_DOWN;
	GPIO_Init(GPIOA, &GPIO_InitStructure);
	/* GPIOA GPIOE Clocks enable */
	GPIO_PinAFConfig(GPIOA, GPIO_PinSource8, GPIO_AF_2); // TIM1_CH1
}
void acmp2_cfg()
{
	GPIO_InitTypeDef GPIO_InitStructure;

	GPIO_InitStructure.GPIO_Pin = GPIO_Pin_5;
	GPIO_InitStructure.GPIO_Mode = GPIO_Mode_AF;
	GPIO_InitStructure.GPIO_Speed = GPIO_Speed_Level_2;
	GPIO_InitStructure.GPIO_OType = GPIO_OType_PP;
	GPIO_Init(GPIOA, &GPIO_InitStructure);
	GPIO_PinAFConfig(GPIOA, GPIO_PinSource5, GPIO_AF_6); ////OUT

	GPIO_InitStructure.GPIO_Pin = GPIO_Pin_1;
	GPIO_InitStructure.GPIO_Mode = GPIO_Mode_AN;
	GPIO_InitStructure.GPIO_Speed = GPIO_Speed_Level_2;
	GPIO_InitStructure.GPIO_OType = GPIO_OType_PP;
	GPIO_Init(GPIOB, &GPIO_InitStructure);
	GPIO_PinAFConfig(GPIOB, GPIO_PinSource1, GPIO_AF_1); // CP2_P_6[0]

	GPIO_InitStructure.GPIO_Pin = GPIO_Pin_6;
	GPIO_InitStructure.GPIO_Mode = GPIO_Mode_AN;
	GPIO_InitStructure.GPIO_Speed = GPIO_Speed_Level_2;
	GPIO_InitStructure.GPIO_OType = GPIO_OType_PP;
	GPIO_Init(GPIOF, &GPIO_InitStructure);
	GPIO_PinAFConfig(GPIOF, GPIO_PinSource6, GPIO_AF_2); // CP2_P_6[1]

	GPIO_InitStructure.GPIO_Pin = GPIO_Pin_6;
	GPIO_InitStructure.GPIO_Mode = GPIO_Mode_AN;
	GPIO_InitStructure.GPIO_Speed = GPIO_Speed_Level_2;
	GPIO_InitStructure.GPIO_OType = GPIO_OType_PP;
	GPIO_Init(GPIOB, &GPIO_InitStructure);
	GPIO_PinAFConfig(GPIOB, GPIO_PinSource6, GPIO_AF_2); ////CP2_N_7[2]

	ACMP_InitTypeDef ACMP_InitStruct;
	ACMP_InitStruct.ACMP_Delay_time = CP_NODelay_time; //输出延迟配置
	ACMP_InitStruct.ACMP_Blanking = CP_NOBLANKING;	   //比较器消隐源选择
	ACMP_InitStruct.ACMP_Is = CP_IS_POS;			   //比较器输出极性
	ACMP_InitStruct.ACMP_HYSEN = DISABLE;			   //迟滞使能配置
	ACMP_InitStruct.ACMP_FREN = ENABLE;				   //快速响应使能
	ACMP_InitStruct.ACMP_FS = DISABLE;				   //输出滤波使能配置

	ACMP_InitStruct.CMP_INTENMASK = ENABLE;				 //比较器连续比较中断使能屏蔽
	ACMP_InitStruct.CMP_SEQ_MODE = ENABLE;				 //连续模式使能
	ACMP_InitStruct.TRIG_MODE = CP_TIRG_EXTEN;			 //触发模式：软件或者外部硬件触发
	ACMP_InitStruct.CHNL_CNT_TIME = CHNL_CNT_TIME_64CLK; //比较器通道切换时钟周期选择

	ACMP_InitStruct.EXTSELECT = ENABLE_EXTSELG0;			  // Two sets of trigger sources enable control bits
	ACMP_InitStruct.EXTEN_Signal_andmode = ENABLE;			  // Trigger signal logic 'or' or 'and'
	ACMP_InitStruct.CP_EXTSP = CP_EXTSP_POS;				  //触发信号极性选择
	ACMP_InitStruct.SYN_MODE = CP_SYN_MODE;					  //外部触发同步或异步
	ACMP_InitStruct.TRIG_SOURCE = TRIG_TIM1_CC1;			  //触发源选择
	ACMP_InitStruct.TRIG_DELAY_TIME = TRIG_DELAY_TIME_128CLK; //外部触发延迟时钟
	ACMP_InitStruct.EXTEN_EDGE_MODE = CP_Edge_model;		  //外部触发信号方式
	ACMP_InitStruct.EXTEN_MODE_SEL = CP_EXTEN_RISE;			  //外部触发模式选择
	ACMP2_Init(&ACMP_InitStruct);
	ACMP2_SEQ_INPUT_SELECT(ENABLE, 3, 2);
	ACMP2_Cmd(ENABLE);
}

int main()
{
	SystemInit();
	SetSysClock();//主频配置
	RCC_APB1PeriphClockCmd(RCC_APB1Periph_ANACTRL, ENABLE);
	RCC_APB1PeriphClockCmd(RCC_APB1Periph_TIM1, ENABLE);
	RCC_AHBPeriphClockCmd(RCC_AHBPeriph_GPIOA, ENABLE);
	RCC_AHBPeriphClockCmd(RCC_AHBPeriph_GPIOB, ENABLE);
	RCC_AHBPeriphClockCmd(RCC_AHBPeriph_GPIOF, ENABLE);

	DAC0_cfg();	 // DAC0_OUT=PA10
	acmp0_cfg(); // PA0(OUT) PA1(P) DAC0(N)/PF0

	acmp1_cfg(); // PA2(OUT) PF1(P)  PA3(P)  PF7(N)

	tim1_cfg_init();
	acmp2_cfg(); // PA5(OUT) PB1(P) PF6(P)  PB6(N)
	while (1)
	{
		SATRT_OFACMP1(); //连续比较软件触发需要配置START，START一次，转换一个序列

		delay(1000);
	}
}

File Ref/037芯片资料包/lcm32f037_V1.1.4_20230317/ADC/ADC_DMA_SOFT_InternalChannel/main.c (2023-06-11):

#include "lcm32f037_conf.h"
#include "lcm32f037.h"
#include "lcm32f037_rcc.h"
#include "lcm32f037_uart.h"
#include "lcm32f037_gpio.h"
#include <stdio.h>
#include <stdlib.h>
#include <string.h>
#include "lcm32f037_div.h"
#include "lcm32f037_adc.h"
#include "lcm32f037_opa.h"
#include "lcm32f037_tim.h"
#include "lcm32f037_dma.h"
#include "lcm32f037_flash.h"
#include "lcm32f037_dac.h"
/**
  ******************************************************************************
  ADC内部通道：
	OPA0O(OP0OEX)=ADCIN[11]/经PA3回环到ADCIN[3];
	OPA0O(OP1OEX)=ADCIN[12]/经PA7回环到ADCIN[7];
	OPA0O(OP2OEX)=ADCIN[2]/经PB1回环到ADCIN[9];

	DAC_OUT0:连接到外部端口PA10的模拟通道2，进而通过同时打开PA10的1通道，可以回环到ADCIN[15]
			 连接到外部端口PA4的模拟通道1，进而通过同时打开PA4的2通道，可以回环到ADCIN[4]

	DAC_OUT1:连接到外部端口PA5的模拟通道2，进而通过同时打开PA4的1通道，可以回环到ADCIN[5]

	温度传感器：当 ST=1，SV=0 时选用 ADC_IN16，其他通道(ADC_IN0~15，ADC_IN17)禁用。
	VDDA：当 ST=1，SV=1时选用 ADC_IN17(VDD)，其他通道(ADC_IN0~15，ADC_IN16)禁用。
  ******************************************************************************/
#define DMA_ENABLE 1
#define ADC_SIZE 9UL
#define ADC1_DR_Address (0x4001A020)
unsigned int ADCConvertedRawData[9] = {0};

void OPA0_Init()
{
	GPIO_InitTypeDef GPIO_InitStruct;
	// OPA0
	GPIO_InitStruct.GPIO_Pin = GPIO_Pin_8;
	GPIO_InitStruct.GPIO_Mode = GPIO_Mode_AN;
	GPIO_InitStruct.GPIO_Speed = GPIO_Speed_Level_2;
	GPIO_InitStruct.GPIO_OType = GPIO_OType_PP;
	GPIO_InitStruct.GPIO_PuPd = GPIO_PuPd_NOPULL;
	GPIO_Init(GPIOA, &GPIO_InitStruct);
	GPIO_PinAFConfig(GPIOA, GPIO_PinSource8, GPIO_AF_2);

	GPIO_InitStruct.GPIO_Pin = GPIO_Pin_9;
	GPIO_InitStruct.GPIO_Mode = GPIO_Mode_AN;
	GPIO_InitStruct.GPIO_Speed = GPIO_Speed_Level_2;
	GPIO_InitStruct.GPIO_OType = GPIO_OType_PP;
	GPIO_InitStruct.GPIO_PuPd = GPIO_PuPd_NOPULL;
	GPIO_Init(GPIOA, &GPIO_InitStruct);
	GPIO_PinAFConfig(GPIOA, GPIO_PinSource9, GPIO_AF_2); //正端输入

	GPIO_InitStruct.GPIO_Pin = GPIO_Pin_3;
	GPIO_InitStruct.GPIO_Mode = GPIO_Mode_AN;
	GPIO_InitStruct.GPIO_Speed = GPIO_Speed_Level_2;
	GPIO_InitStruct.GPIO_OType = GPIO_OType_PP;
	GPIO_InitStruct.GPIO_PuPd = GPIO_PuPd_NOPULL;
	GPIO_Init(GPIOA, &GPIO_InitStruct);
	//	GPIO_PinAFConfig(GPIOA,GPIO_PinSource3,GPIO_AF_2);//opa0输出到PA3 可以测量
	GPIO_PinAFConfig(GPIOA, GPIO_PinSource3, GPIO_AF_1 | GPIO_AF_2); //通过PA3回环使OP0O接到ADCIN[3];OP0O内部直连ADCIN[11]

	OPA_InitTypeDef OPA_InitStruct;
	OPA_InitStruct.OPA_Oppselect = OPA0_Oppselect_PA9;
	OPA_InitStruct.OPA_Opnselect = OPA0_Opnselect_PA8;
	OPA_InitStruct.OPA_Gain = OPA_Gain_10;
	OPA_InitStruct.OPA_BiasVoltage = OPA_BiasVoltage_DISEN;
	OPA_InitStruct.OPA_FeedbackRes = OPA_FeedbackRes_EN;
	OPA_InitStruct.OPA_Opoto_Gpio = OPA_OPOEX_EN;
	OPA_InitStruct.OPA_OppRES_short = OPA_OppRES_short_DISEN;
	OPA_InitStruct.OPA_OpnRES_short = OPA_OpnRES_short_DISEN;
	OPA_InitStruct.OPA_BiasVoltageSource = OPA_OPA_BiasVoltageSource_HALFVRH;
	OPA_Init(OPA0, &OPA_InitStruct);
	OPA_Cmd(OPA0, ENABLE);
}
void OPA1_Init()
{
	GPIO_InitTypeDef GPIO_InitStruct;
	//	//OPA1
	GPIO_InitStruct.GPIO_Pin = GPIO_Pin_1;
	GPIO_InitStruct.GPIO_Mode = GPIO_Mode_AN;
	GPIO_InitStruct.GPIO_Speed = GPIO_Speed_Level_2;
	GPIO_InitStruct.GPIO_OType = GPIO_OType_PP;
	GPIO_InitStruct.GPIO_PuPd = GPIO_PuPd_NOPULL;
	GPIO_Init(GPIOF, &GPIO_InitStruct);
	GPIO_PinAFConfig(GPIOF, GPIO_PinSource1, GPIO_AF_1);

	GPIO_InitStruct.GPIO_Pin = GPIO_Pin_6;
	GPIO_InitStruct.GPIO_Mode = GPIO_Mode_AN;
	GPIO_InitStruct.GPIO_Speed = GPIO_Speed_Level_2;
	GPIO_InitStruct.GPIO_OType = GPIO_OType_PP;
	GPIO_InitStruct.GPIO_PuPd = GPIO_PuPd_NOPULL;
	GPIO_Init(GPIOA, &GPIO_InitStruct);
	GPIO_PinAFConfig(GPIOA, GPIO_PinSource6, GPIO_AF_2); //正端输入

	GPIO_InitStruct.GPIO_Pin = GPIO_Pin_7;
	GPIO_InitStruct.GPIO_Mode = GPIO_Mode_AN;
	GPIO_InitStruct.GPIO_Speed = GPIO_Speed_Level_2;
	GPIO_InitStruct.GPIO_OType = GPIO_OType_PP;
	GPIO_InitStruct.GPIO_PuPd = GPIO_PuPd_NOPULL;
	GPIO_Init(GPIOA, &GPIO_InitStruct);
	//	GPIO_PinAFConfig(GPIOA,GPIO_PinSource7,GPIO_AF_2);//opa1输出到PA7 可以测量
	GPIO_PinAFConfig(GPIOA, GPIO_PinSource7, GPIO_AF_1 | GPIO_AF_2); //通过PA7回环使OP1O接到ADCIN[7];OP1O内部直连ADCIN[12]

	OPA_InitTypeDef OPA_InitStruct;
	OPA_InitStruct.OPA_Oppselect = OPA1_Oppselect_PA6;
	OPA_InitStruct.OPA_Opnselect = OPA1_Opnselect_PF1;
	OPA_InitStruct.OPA_Gain = OPA_Gain_10;
	OPA_InitStruct.OPA_BiasVoltage = OPA_BiasVoltage_DISEN;
	OPA_InitStruct.OPA_FeedbackRes = OPA_FeedbackRes_EN;
	OPA_InitStruct.OPA_Opoto_Gpio = OPA_OPOEX_EN;
	OPA_InitStruct.OPA_OppRES_short = OPA_OppRES_short_DISEN;
	OPA_InitStruct.OPA_OpnRES_short = OPA_OpnRES_short_DISEN;
	OPA_InitStruct.OPA_BiasVoltageSource = OPA_OPA_BiasVoltageSource_HALFVRH;
	OPA_Init(OPA1, &OPA_InitStruct);
	OPA_Cmd(OPA1, ENABLE);
}
void OPA2_Init()
{
	GPIO_InitTypeDef GPIO_InitStruct;
	// OPA2
	GPIO_InitStruct.GPIO_Pin = GPIO_Pin_7;
	GPIO_InitStruct.GPIO_Mode = GPIO_Mode_AN;
	GPIO_InitStruct.GPIO_Speed = GPIO_Speed_Level_2;
	GPIO_InitStruct.GPIO_OType = GPIO_OType_PP;
	GPIO_InitStruct.GPIO_PuPd = GPIO_PuPd_NOPULL;
	GPIO_Init(GPIOB, &GPIO_InitStruct);
	GPIO_PinAFConfig(GPIOB, GPIO_PinSource7, GPIO_AF_2);

	GPIO_InitStruct.GPIO_Pin = GPIO_Pin_0;
	GPIO_InitStruct.GPIO_Mode = GPIO_Mode_AN;
	GPIO_InitStruct.GPIO_Speed = GPIO_Speed_Level_2;
	GPIO_InitStruct.GPIO_OType = GPIO_OType_PP;
	GPIO_InitStruct.GPIO_PuPd = GPIO_PuPd_NOPULL;
	GPIO_Init(GPIOB, &GPIO_InitStruct);
	GPIO_PinAFConfig(GPIOB, GPIO_PinSource0, GPIO_AF_2); //正端输入

	GPIO_InitStruct.GPIO_Pin = GPIO_Pin_1;
	GPIO_InitStruct.GPIO_Mode = GPIO_Mode_AN;
	GPIO_InitStruct.GPIO_Speed = GPIO_Speed_Level_2;
	GPIO_InitStruct.GPIO_OType = GPIO_OType_PP;
	GPIO_InitStruct.GPIO_PuPd = GPIO_PuPd_NOPULL;
	GPIO_Init(GPIOB, &GPIO_InitStruct);
	//	GPIO_PinAFConfig(GPIOB,GPIO_PinSource1,GPIO_AF_2);//opa2输出到PB1 可以测量
	GPIO_PinAFConfig(GPIOB, GPIO_PinSource1, GPIO_AF_1 | GPIO_AF_2); //通过PB1回环使OP2O接到ADCIN[9];OP0O内部直连ADCIN[2]

	OPA_InitTypeDef OPA_InitStruct;
	OPA_InitStruct.OPA_Oppselect = OPA2_Oppselect_PB0;
	OPA_InitStruct.OPA_Opnselect = OPA2_Opnselect_PB7;
	OPA_InitStruct.OPA_Gain = OPA_Gain_10;
	OPA_InitStruct.OPA_BiasVoltage = OPA_BiasVoltage_DISEN;
	OPA_InitStruct.OPA_FeedbackRes = OPA_FeedbackRes_EN;
	OPA_InitStruct.OPA_Opoto_Gpio = OPA_OPOEX_EN;
	OPA_InitStruct.OPA_OppRES_short = OPA_OppRES_short_DISEN;
	OPA_InitStruct.OPA_OpnRES_short = OPA_OpnRES_short_DISEN;
	OPA_InitStruct.OPA_BiasVoltageSource = OPA_OPA_BiasVoltageSource_HALFVRH;
	OPA_Init(OPA2, &OPA_InitStruct);
	OPA_Cmd(OPA2, ENABLE);
}
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

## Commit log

2023-02-07 add bldc hall sensor support
2023-02-08 fix bug of zero ctrl
    [main.c, variable.c]
2023-02-08 bldc snesorless support speed control
2023-02-08 add mcsdk support for pmsm motor of 48v
2023-02-11 modify parameter of mcsdk for 48v pump
2023-02-11 create hardware for 48v pmsm
    [01_Power.SchDoc, 02_Sensor.SchDoc, 03_MOS_Drive.SchDoc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]
2023-02-12 add sch for hardware
    [01_Power.SchDoc, 02_Sensor.SchDoc, 03_MOS_Drive.SchDoc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]
2023-02-13 save best parameter,time:2023-2-13
    [PMSM_SBC.PrjPcb]
2023-02-20 first add gui
    [02_Sensor.SchDoc]
2023-02-20 update pcb
    [01_Power.SchDoc, 02_Sensor.SchDoc, 03_MOS_Drive.SchDoc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]
2023-02-21 update gui code
    [PMSM_SBC.PrjPcb]
2023-02-21 fix pcb bug of panel
2023-03-21 update fortior code
    [FT-QR-AE-01-A1 客户方案性能设计需求表.xlsx, FT-QR-AE-02-A0 应用方案开发进度表.xlsx, FU-AM-FU6861-B-025-HW-V1.0-20210601.SCHDOC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]
2023-03-21 update fortior datasheet
    [FU-AM-FU6861-B-025-HW-V1.0-20210601.pcbdoc, FU-AM-FU6861Q-B-002-HW-V3.0-20200620.SchDoc]
2023-03-21 add fortior hardware
    [01_Power.SchDoc, 02_MCU.SchDoc, 03_Mos.SchDoc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]
2023-03-22 update fortior pcb
    [01_Power.SchDoc, 02_MCU.SchDoc, 03_Mos.SchDoc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]
2023-03-22 add pdf of fortior
    [03_Mos.SchDoc, 04_Sensor.SchDoc, FU-AM-FU6861Q-B-002-HW-V3.0-20200620.PcbDoc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]
2023-03-22 update pcb of fortior
    [02_MCU.SchDoc, 03_Mos.SchDoc, 04_Sensor.SchDoc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]
2023-03-27 update tm1650 driver for fortior fu6861q
    [01_Power.SchDoc, 02_MCU.SchDoc]
2023-04-01 store version:2023-4-1
    [FT-QR-AE-01-A1 客户方案性能设计需求表.xlsx, FT-QR-AE-02-A0 应用方案开发进度表.xlsx, FU-AM-FU6861Q-B-002-HW-V3.0-20200620.PcbDoc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]
2023-04-01 update ignore and save version:2023-4-1
    [ADC.obj, AMP.obj, AddFunction.obj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]
2023-04-01 Fixed speed regulation unable to limit the interval
    [ADC.obj, AMP.obj, AddFunction.obj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]
2023-04-04 store version:2023-4-4
    [01_Power.SchDoc, PMSM_ShowV0.2.PrjPcb]
2023-05-05 修改README，增加领芯水泵方案硬件图纸
    [01_Power.SchDoc, 02_MCU.SchDoc, 03_Mos.SchDoc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]
2023-05-15 [修改描述]：增加领芯方案
    [01_Power.SchDoc]
2023-05-17 [修改描述]：提供调速接口、设计全局状态变量、提供任务接口
    [01_Power.SchDoc, 02_MCU.SchDoc, 03_Mos.SchDoc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]
2023-05-17 [修改描述]：修复TM1650按键读取BUG，增加母线电流读取，更新UI显示
2023-05-20 [修改描述]：软件IIC-SDA修正为OD，错误逻辑修改为手动ACK，增加缺相与过流保护
    [02_MCU.SchDoc, 03_Mos.SchDoc, PMSM_LCP037.PrjPcb]
2023-06-11 [修改描述]：添加领芯SDK代码，增加电流采集功能，关闭母线采样
    [03_Mos.SchDoc, A-水泵_LCP037BK32ET8-48V-SCH-V1.2-20230321.SchDoc, D-水泵-V1.2-BOM.xlsx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]
2023-10-12 [修改描述]：基于LCP HardWare V0.3进行功能验证，测试自启方案。
    [01_Power.SchDoc, 02_MCU.SchDoc, 03_Mos.SchDoc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]
2023-11-28 support new control logic
    [01_Panel.SchDoc, A-水泵_LCP037BK32ET8-48V-SCH-V1.2-20230321.SchDoc, D-水泵-V1.2-BOM.xlsx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]
2024-01-24 fix lcm foc
    [01_Power.SchDoc, 02_MCU.SchDoc, 03_Mos.SchDoc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]
2024-03-22 pump: change over voltage to 90v
